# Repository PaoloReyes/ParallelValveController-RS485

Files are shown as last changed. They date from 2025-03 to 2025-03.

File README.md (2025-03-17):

# Parallel Valve Controller RS485 - README

## Overview
This repository contains the hardware and software needed to build a 20 container controller under freertos SMP multicore architecture on UART ISR event driven processes for ESP32-S3.
The controller is responsible for listening to RS485 messages and actuate the connected containers accordingly.

## Features
- **Parallel Control**: Uses two XTensa LX7 Cores under freertos on container independent tasks.
- **Reduces PLC overhead**: PID control is performed under the ESP32-S3 and not the main PLC logic.
- **Communication**: Interfaces with the main controller via RS485 communication.

## Communication Protocol
The car module receives and sends commands via a predefined protocol:
- `OP #` - Opens the controller based on its id number #.
- `CL` - Immediately closes the RS485 communication with the controller.
- `AD` - Returns the current id of the controller.
- `AD #` - Assigns the number # as the controller id.
- `WP` - Makes the AD # command to take effect and needs a reboot.
- `CV #1 #2 #3` - Performs a control update on the specified #1 container, #2 with the current weight and #3 the weight setpoint

## Hardware
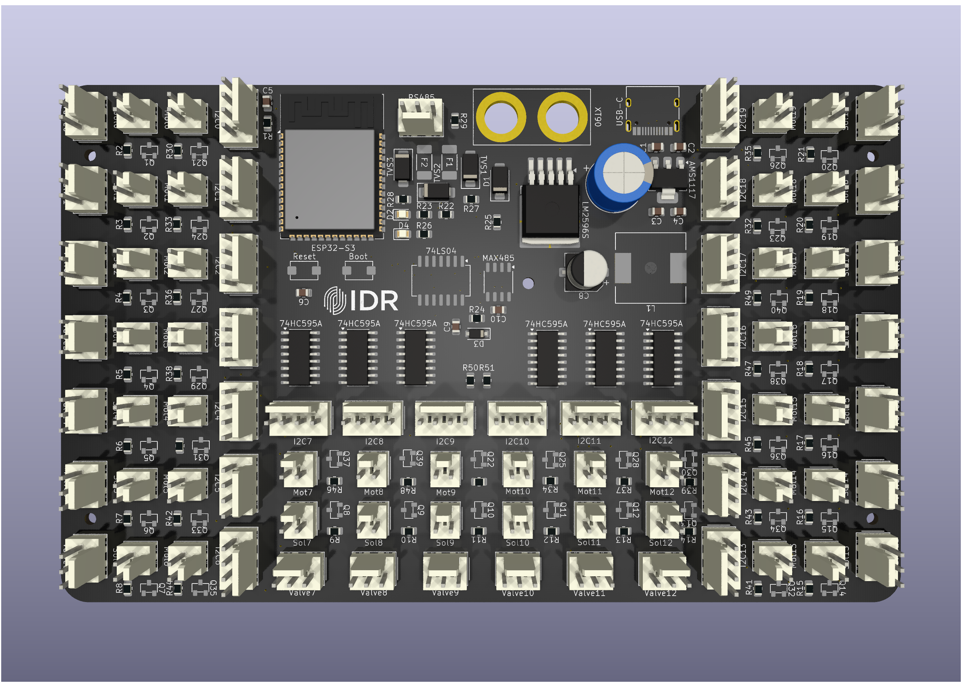
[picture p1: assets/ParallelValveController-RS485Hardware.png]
Hardware


## Software Architecture
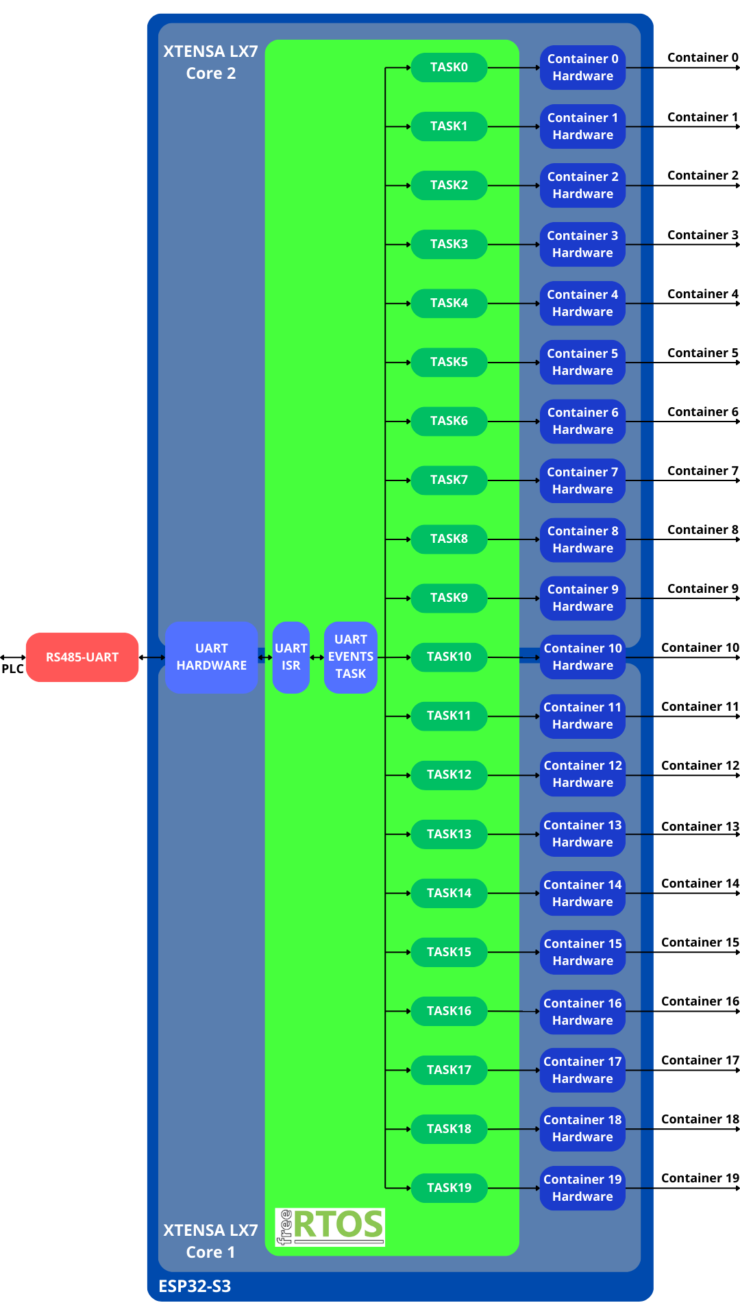
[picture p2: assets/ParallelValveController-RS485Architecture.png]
Controller


## FSM
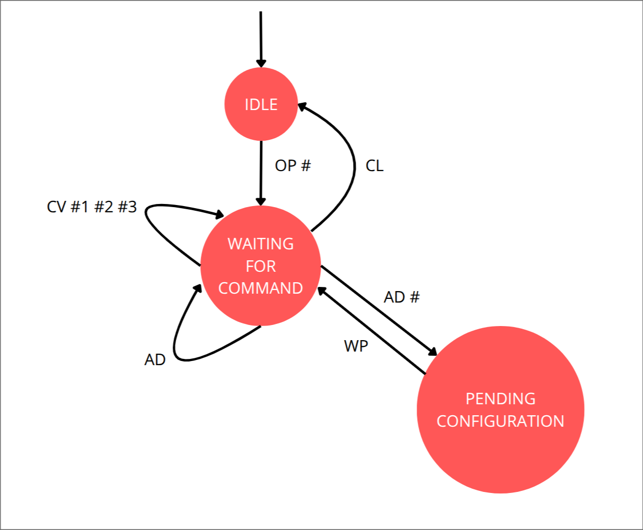
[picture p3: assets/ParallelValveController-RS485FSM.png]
FSM


## Troubleshooting
| Issue | Possible Cause | Solution |
|---|---|---|
| Valve not moving | Loose wiring, wrong valve firmware | Check connections, update your valve firmware |
| Solenoid not actuating | Loose wiring | Check connections |
| Motor not mixing | Loose wiring | Check connections |
| Container weight not available | Loose wiring, wrong digitalizer firmware | Check connections, update your valve firmware 
| No response | Communication failure, wrong firmware | Verify RS485 wiring and settings, update the controller firmware |

## Contributors
- **Paolo Reyes** - Lead Developer

## License
This project is licensed under the MIT License - see the LICENSE file for details.

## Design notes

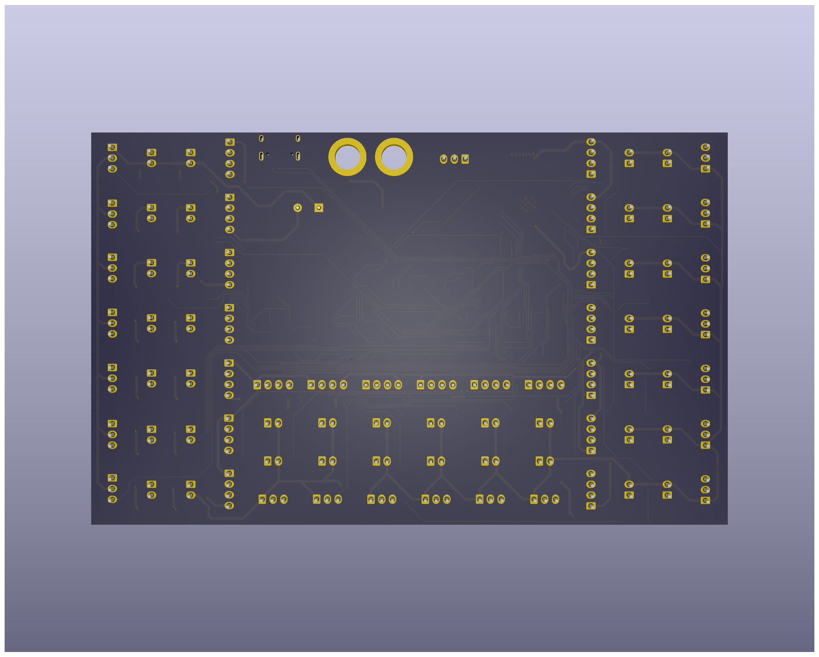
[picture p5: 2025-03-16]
Hardware/Renders/PreliminarBack.png

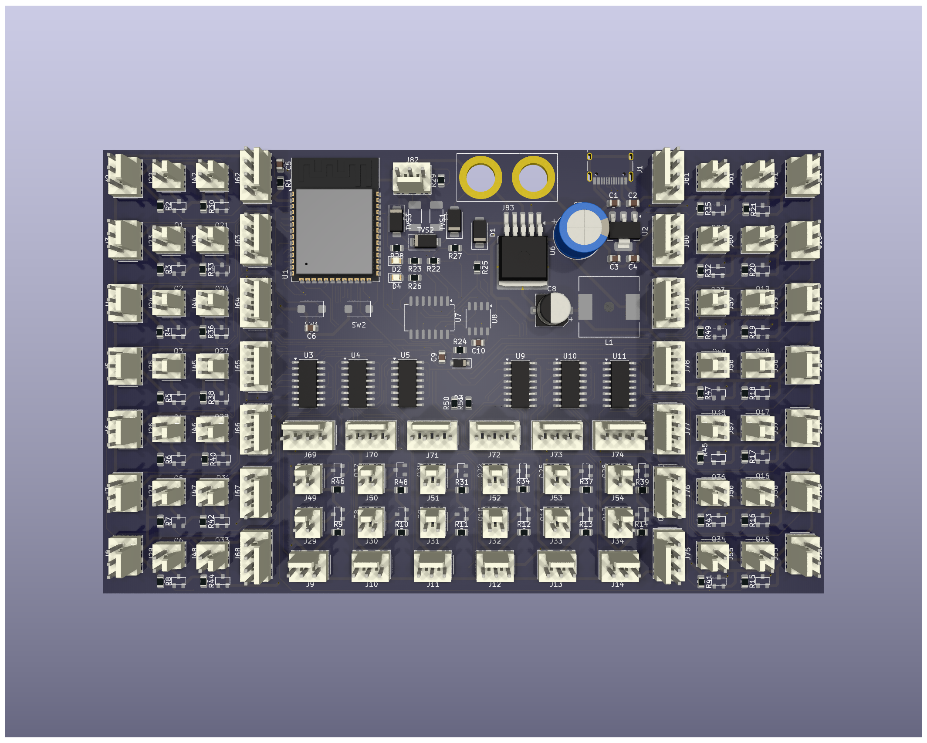
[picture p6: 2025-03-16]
Hardware/Renders/PreliminarFront.png

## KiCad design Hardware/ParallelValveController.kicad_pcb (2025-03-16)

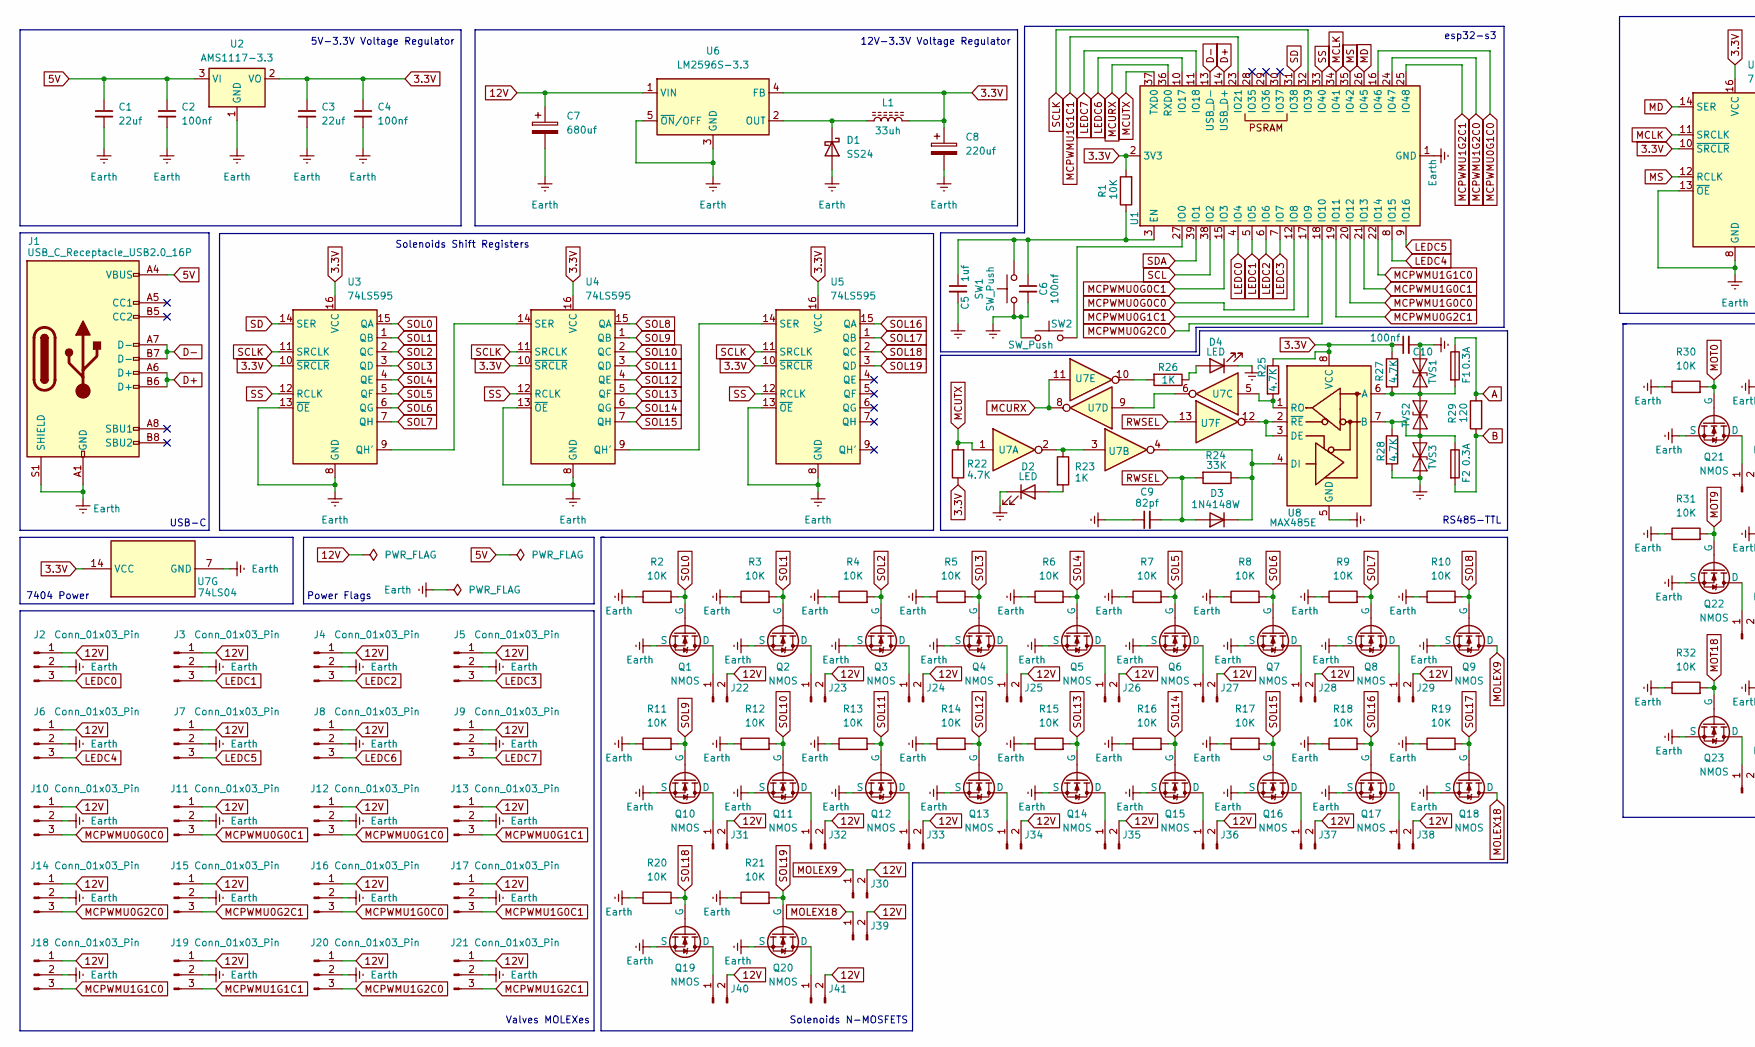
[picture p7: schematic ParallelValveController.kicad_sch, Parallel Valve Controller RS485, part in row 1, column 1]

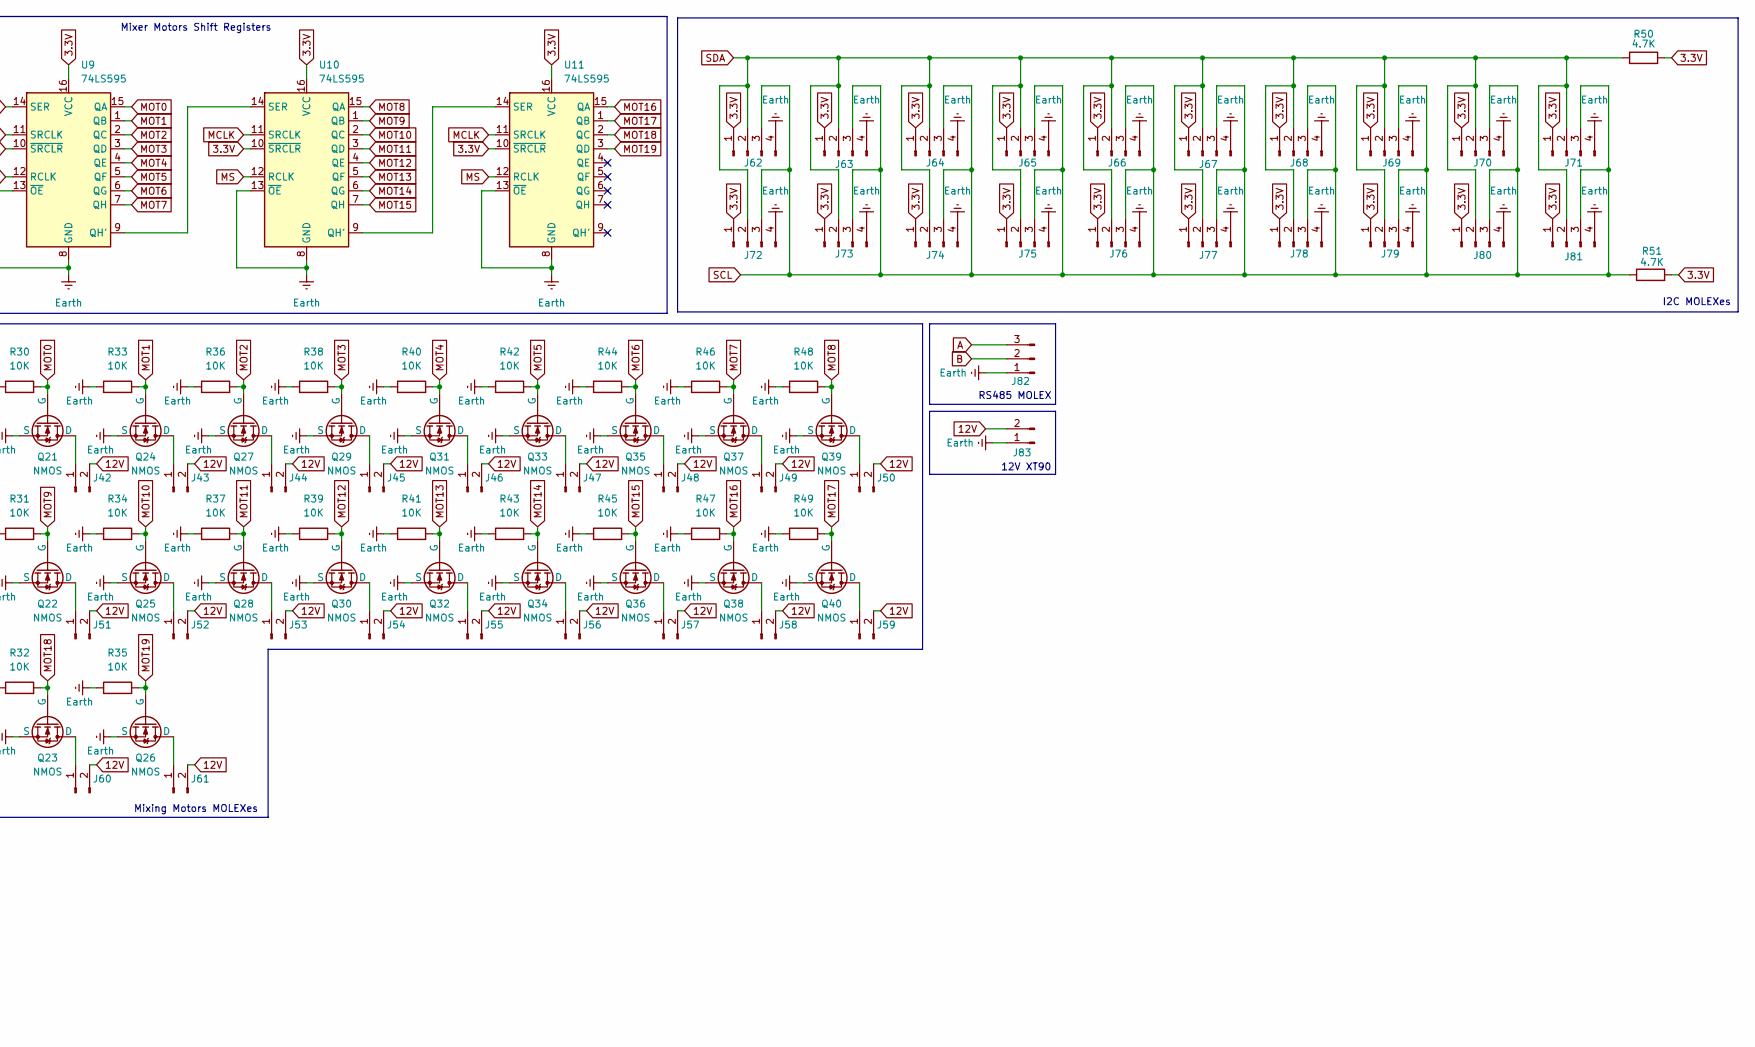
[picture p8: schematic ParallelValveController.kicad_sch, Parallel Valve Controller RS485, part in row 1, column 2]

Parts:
C1, C3: 22uf; C_0805_2012Metric
C2, C4, C6, C10: 100nf; C_0805_2012Metric
C5: 1uf; C_0805_2012Metric
C7: 680uf; CP_Radial_D10.0mm_P5.00mm
C8: 220uf; CP_Elec_6.3x7.7
C9: 82pf; C_0805_2012Metric
D1: SS24; D_SMA
D2, D4: LED; LED_0805_2012Metric
D3: 1N4148W; D_SOD-123
F1, F2: 0.3A; Fuse_2010_5025Metric_Pad1.52x2.65mm_HandSolder
J1: USB_C_Receptacle_USB2.0_16P; USB_C_Receptacle_HRO_TYPE-C-31-M-12
J2, J3, J4, J5, J6, J7, J8, J9, J10, J11, J12, J13, J14, J15, J16, J17, J18, J19, J20, J21, J82: Conn_01x03_Pin; Molex_KK-254_AE-6410-03A_1x03_P2.54mm_Vertical
J22, J23, J24, J25, J26, J27, J28, J29, J30, J31, J32, J33, J34, J35, J36, J37, J38, J39, J40, J41, J42, J43, J44, J45, J46, J47, J48, J49, J50, J51, J52, J53, J54, J55, J56, J57, J58, J59, J60, J61: Conn_01x02_Pin; Molex_KK-254_AE-6410-02A_1x02_P2.54mm_Vertical
J62, J63, J64, J65, J66, J67, J68, J69, J70, J71, J72, J73, J74, J75, J76, J77, J78, J79, J80, J81: Conn_01x02_Pin; Molex_KK-254_AE-6410-04A_1x04_P2.54mm_Vertical
J83: Conn_01x02_Pin; XT90-Female
L1: 33uh; L_12x12mm_H8mm
Q1, Q2, Q3, Q4, Q5, Q6, Q7, Q8, Q9, Q10, Q11, Q12, Q13, Q14, Q15, Q16, Q17, Q18, Q19, Q20, Q21, Q22, Q23, Q24, Q25, Q26, Q27, Q28, Q29, Q30, Q31, Q32, Q33, Q34, Q35, Q36, Q37, Q38, Q39, Q40: NMOS; SI2302
R1, R2, R3, R4, R5, R6, R7, R8, R9, R10, R11, R12, R13, R14, R15, R16, R17, R18, R19, R20, R21, R30, R31, R32, R33, R34, R35, R36, R37, R38, R39, R40, R41, R42, R43, R44, R45, R46, R47, R48, R49: 10K; R_0805_2012Metric
R22, R25, R27, R28, R50, R51: 4.7K; R_0805_2012Metric
R23, R26: 1K; R_0805_2012Metric
R24: 33K; R_0805_2012Metric
R29: 120; R_0805_2012Metric
SW1, SW2: SW_Push; MicroSwtich3x4x2mm
TVS1: SMAJ6.8CA; D_SMA
TVS2, TVS3: SMAJ6.5CA; D_SMA
U1: ESP32-S3-WROOM-1
U2: AMS1117-3.3; SOT-223-3_TabPin2
U3, U4, U5, U9, U10, U11: 74LS595; SOP-16_3.9x9.9mm_P1.27mm
U6: LM2596S-3.3; TO-263-5_TabPin3
U7: 74LS04; SO-14_5.3x10.2mm_P1.27mm
U8: MAX485E; SOP-8_3.9x4.9mm_P1.27mm

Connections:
3.3V: C3.1, C4.1, C8.1, C10.1, J62.1, J63.1, J64.1, J65.1, J66.1, J67.1, J68.1, J69.1, J70.1, J71.1, J72.1, J73.1, J74.1, J75.1, J76.1, J77.1, J78.1, J79.1, J80.1, J81.1, L1.2, R1.2, R22.1, R25.1, R27.1, R50.2, R51.2, U1.2 (3V3), U2.2 (VO), U3.10 (~SRCLR), U3.16 (VCC), U4.10 (~SRCLR), U4.16 (VCC), U5.10 (~SRCLR), U5.16 (VCC), U6.4 (FB), U7.14 (VCC), U8.8 (VCC), U9.10 (~SRCLR), U9.16 (VCC), U10.10 (~SRCLR), U10.16 (VCC), U11.10 (~SRCLR), U11.16 (VCC)
5V: C1.1, C2.1, J1.A4 (VBUS), J1.A9 (VBUS), J1.B4 (VBUS), J1.B9 (VBUS), U2.3 (VI)
12V: C7.1, J2.1, J3.1, J4.1, J5.1, J6.1, J7.1, J8.1, J9.1, J10.1, J11.1, J12.1, J13.1, J14.1, J15.1, J16.1, J17.1, J18.1, J19.1, J20.1, J21.1, J22.2, J23.2, J24.2, J25.2, J26.2, J27.2, J28.2, J29.2, J30.2, J31.2, J32.2, J33.2, J34.2, J35.2, J36.2, J37.2, J38.2, J39.2, J40.2, J41.2, J42.2, J43.2, J44.2, J45.2, J46.2, J47.2, J48.2, J49.2, J50.2, J51.2, J52.2, J53.2, J54.2, J55.2, J56.2, J57.2, J58.2, J59.2, J60.2, J61.2, J83.2, U6.1 (VIN)
A: F1.1, J82.3, R29.2
B: F2.2, J82.2, R29.1
D+: J1.A6 (D+), J1.B6 (D+), U1.14 (USB_D+)
D-: J1.A7 (D-), J1.B7 (D-), U1.13 (USB_D-)
Earth: C1.2, C2.2, C3.2, C4.2, C5.2, C6.2, C7.2, C8.2, C9.1, C10.2, D1.2 (A), D2.1 (K), D4.1 (K), J1.A1 (GND), J1.A12 (GND), J1.B1 (GND), J1.B12 (GND), J1.S1 (SHIELD), J2.2, J3.2, J4.2, J5.2, J6.2, J7.2, J8.2, J9.2, J10.2, J11.2, J12.2, J13.2, J14.2, J15.2, J16.2, J17.2, J18.2, J19.2, J20.2, J21.2, J62.4, J63.4, J64.4, J65.4, J66.4, J67.4, J68.4, J69.4, J70.4, J71.4, J72.4, J73.4, J74.4, J75.4, J76.4, J77.4, J78.4, J79.4, J80.4, J81.4, J82.1, J83.1, Q1.3 (S), Q2.3 (S), Q3.3 (S), Q4.3 (S), Q5.3 (S), Q6.3 (S), Q7.3 (S), Q8.3 (S), Q9.3 (S), Q10.3 (S), Q11.3 (S), Q12.3 (S), Q13.3 (S), Q14.3 (S), Q15.3 (S), Q16.3 (S), Q17.3 (S), Q18.3 (S), Q19.3 (S), Q20.3 (S), Q21.3 (S), Q22.3 (S), Q23.3 (S), Q24.3 (S), Q25.3 (S), Q26.3 (S), Q27.3 (S), Q28.3 (S), Q29.3 (S), Q30.3 (S), Q31.3 (S), Q32.3 (S), Q33.3 (S), Q34.3 (S), Q35.3 (S), Q36.3 (S), Q37.3 (S), Q38.3 (S), Q39.3 (S), Q40.3 (S), R2.1, R3.1, R4.1, R5.1, R6.1, R7.1, R8.1, R9.1, R10.1, R11.1, R12.1, R13.1, R14.1, R15.1, R16.1, R17.1, R18.1, R19.1, R20.1, R21.1, R28.2, R30.1, R31.1, R32.1, R33.1, R34.1, R35.1, R36.1, R37.1, R38.1, R39.1, R40.1, R41.1, R42.1, R43.1, R44.1, R45.1, R46.1, R47.1, R48.1, R49.1, SW1.1, SW2.1, TVS1.2 (A2), TVS3.1 (A1), U1.1 (GND), U1.40 (GND), U1.41 (GND), U2.1 (GND), U3.8 (GND), U3.13 (~OE), U4.8 (GND), U4.13 (~OE), U5.8 (GND), U5.13 (~OE), U6.3 (GND), U6.5 (~ON/OFF), U7.7 (GND), U8.5 (GND), U9.8 (GND), U9.13 (~OE), U10.8 (GND), U10.13 (~OE), U11.8 (GND), U11.13 (~OE)
LEDC0: J2.3, U1.4 (IO4)
LEDC1: J3.3, U1.5 (IO5)
LEDC2: J4.3, U1.6 (IO6)
LEDC3: J5.3, U1.7 (IO7)
LEDC4: J6.3, U1.8 (IO15)
LEDC5: J7.3, U1.9 (IO16)
LEDC6: J8.3, U1.10 (IO17)
LEDC7: J9.3, U1.11 (IO18)
MCLK: U1.34 (IO41), U9.11 (SRCLK), U10.11 (SRCLK), U11.11 (SRCLK)
MCPWMU0G0C0: J10.3, U1.12 (IO8)
MCPWMU0G0C1: J11.3, U1.15 (IO3)
MCPWMU0G1C0: J12.3, U1.16 (IO46)
MCPWMU0G1C1: J13.3, U1.17 (IO9)
MCPWMU0G2C0: J14.3, U1.18 (IO10)
MCPWMU0G2C1: J15.3, U1.19 (IO11)
MCPWMU1G0C0: J16.3, U1.20 (IO12)
MCPWMU1G0C1: J17.3, U1.21 (IO13)
MCPWMU1G1C0: J18.3, U1.22 (IO14)
MCPWMU1G1C1: J19.3, U1.23 (IO21)
MCPWMU1G2C0: J20.3, U1.24 (IO47)
MCPWMU1G2C1: J21.3, U1.25 (IO48)
MCURX: U1.36 (RXD0), U7.8, U7.11
MCUTX: R22.2, U1.37 (TXD0), U7.1
MD: U1.26 (IO45), U9.14 (SER)
MOLEX9: J30.1, Q9.1 (D)
MOLEX18: J39.1, Q18.1 (D)
MOT0: Q21.2 (G), R30.2, U9.15 (QA)
MOT1: Q24.2 (G), R33.2, U9.1 (QB)
MOT2: Q27.2 (G), R36.2, U9.2 (QC)
MOT3: Q29.2 (G), R38.2, U9.3 (QD)
MOT4: Q31.2 (G), R40.2, U9.4 (QE)
MOT5: Q33.2 (G), R42.2, U9.5 (QF)
MOT6: Q35.2 (G), R44.2, U9.6 (QG)
MOT7: Q37.2 (G), R46.2, U9.7 (QH)
MOT8: Q39.2 (G), R48.2, U10.15 (QA)
MOT9: Q22.2 (G), R31.2, U10.1 (QB)
MOT10: Q25.2 (G), R34.2, U10.2 (QC)
MOT11: Q28.2 (G), R37.2, U10.3 (QD)
MOT12: Q30.2 (G), R39.2, U10.4 (QE)
MOT13: Q32.2 (G), R41.2, U10.5 (QF)
MOT14: Q34.2 (G), R43.2, U10.6 (QG)
MOT15: Q36.2 (G), R45.2, U10.7 (QH)
MOT16: Q38.2 (G), R47.2, U11.15 (QA)
MOT17: Q40.2 (G), R49.2, U11.1 (QB)
MOT18: Q23.2 (G), R32.2, U11.2 (QC)
MOT19: Q26.2 (G), R35.2, U11.3 (QD)
MS: U1.35 (IO42), U9.12 (RCLK), U10.12 (RCLK), U11.12 (RCLK)
unnamed: D1.1 (K), L1.1, U6.2 (OUT)
unnamed: D2.2 (A), R23.2
unnamed: D3.1 (K), R24.1, U7.4, U8.4 (DI)
unnamed: D4.2 (A), R26.1
unnamed: J22.1, Q1.1 (D)
unnamed: J23.1, Q2.1 (D)
unnamed: J24.1, Q3.1 (D)
unnamed: J25.1, Q4.1 (D)
unnamed: J26.1, Q5.1 (D)
unnamed: J27.1, Q6.1 (D)
unnamed: J28.1, Q7.1 (D)
unnamed: J29.1, Q8.1 (D)
unnamed: J31.1, Q10.1 (D)
unnamed: J32.1, Q11.1 (D)
unnamed: J33.1, Q12.1 (D)
unnamed: J34.1, Q13.1 (D)
unnamed: J35.1, Q14.1 (D)
unnamed: J36.1, Q15.1 (D)
unnamed: J37.1, Q16.1 (D)
unnamed: J38.1, Q17.1 (D)
unnamed: J40.1, Q19.1 (D)
unnamed: J41.1, Q20.1 (D)
unnamed: J42.1, Q21.1 (D)
unnamed: J43.1, Q24.1 (D)
unnamed: J44.1, Q27.1 (D)
unnamed: J45.1, Q29.1 (D)
unnamed: J46.1, Q31.1 (D)
unnamed: J47.1, Q33.1 (D)
unnamed: J48.1, Q35.1 (D)
unnamed: J49.1, Q37.1 (D)
unnamed: J50.1, Q39.1 (D)
unnamed: J51.1, Q22.1 (D)
unnamed: J52.1, Q25.1 (D)
unnamed: J53.1, Q28.1 (D)
unnamed: J54.1, Q30.1 (D)
unnamed: J55.1, Q32.1 (D)
unnamed: J56.1, Q34.1 (D)
unnamed: J57.1, Q36.1 (D)
unnamed: J58.1, Q38.1 (D)
unnamed: J59.1, Q40.1 (D)
unnamed: J60.1, Q23.1 (D)
unnamed: J61.1, Q26.1 (D)
unnamed: R23.1, U7.2, U7.3
unnamed: R26.2, U7.10
unnamed: F1.2, R27.2, TVS1.1 (A1), TVS2.2 (A2), U8.6 (A)
unnamed: F2.1, R28.1, TVS2.1 (A1), TVS3.2 (A2), U8.7 (B)
unnamed: C5.1, C6.1, R1.1, SW1.2, U1.3 (EN)
unnamed: SW2.2, U1.27 (IO0)
unnamed: U3.9 (QH'), U4.14 (SER)
unnamed: U4.9 (QH'), U5.14 (SER)
unnamed: U7.6, U7.9
unnamed: U7.12, U8.2 (~RE), U8.3 (DE)
unnamed: R25.2, U7.5, U8.1 (RO)
unnamed: U10.9 (QH'), U11.14 (SER)
unnamed: U9.9 (QH'), U10.14 (SER)
RWSEL: C9.2, D3.2 (A), R24.2, U7.13
SCL: J62.3, J63.3, J64.3, J65.3, J66.3, J67.3, J68.3, J69.3, J70.3, J71.3, J72.3, J73.3, J74.3, J75.3, J76.3, J77.3, J78.3, J79.3, J80.3, J81.3, R51.1, U1.38 (IO2)
SCLK: U1.32 (IO39), U3.11 (SRCLK), U4.11 (SRCLK), U5.11 (SRCLK)
SD: U1.31 (IO38), U3.14 (SER)
SDA: J62.2, J63.2, J64.2, J65.2, J66.2, J67.2, J68.2, J69.2, J70.2, J71.2, J72.2, J73.2, J74.2, J75.2, J76.2, J77.2, J78.2, J79.2, J80.2, J81.2, R50.1, U1.39 (IO1)
SOL0: Q1.2 (G), R2.2, U3.15 (QA)
SOL1: Q2.2 (G), R3.2, U3.1 (QB)
SOL2: Q3.2 (G), R4.2, U3.2 (QC)
SOL3: Q4.2 (G), R5.2, U3.3 (QD)
SOL4: Q5.2 (G), R6.2, U3.4 (QE)
SOL5: Q6.2 (G), R7.2, U3.5 (QF)
SOL6: Q7.2 (G), R8.2, U3.6 (QG)
SOL7: Q8.2 (G), R9.2, U3.7 (QH)
SOL8: Q9.2 (G), R10.2, U4.15 (QA)
SOL9: Q10.2 (G), R11.2, U4.1 (QB)
SOL10: Q11.2 (G), R12.2, U4.2 (QC)
SOL11: Q12.2 (G), R13.2, U4.3 (QD)
SOL12: Q13.2 (G), R14.2, U4.4 (QE)
SOL13: Q14.2 (G), R15.2, U4.5 (QF)
SOL14: Q15.2 (G), R16.2, U4.6 (QG)
SOL15: Q16.2 (G), R17.2, U4.7 (QH)
SOL16: Q17.2 (G), R18.2, U5.15 (QA)
SOL17: Q18.2 (G), R19.2, U5.1 (QB)
SOL18: Q19.2 (G), R20.2, U5.2 (QC)
SOL19: Q20.2 (G), R21.2, U5.3 (QD)
SS: U1.33 (IO40), U3.12 (RCLK), U4.12 (RCLK), U5.12 (RCLK)

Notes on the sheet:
Solenoids Shift Registers
USB-C
RS485-TTL
Mixer Motors Shift Registers
RS485 MOLEX
12V XT90
esp32-s3
Valves MOLEXes
Mixing Motors MOLEXes
7404 Power
I2C MOLEXes
Power Flags
5V-3.3V Voltage Regulator
12V-3.3V Voltage Regulator
Solenoids N-MOSFETS

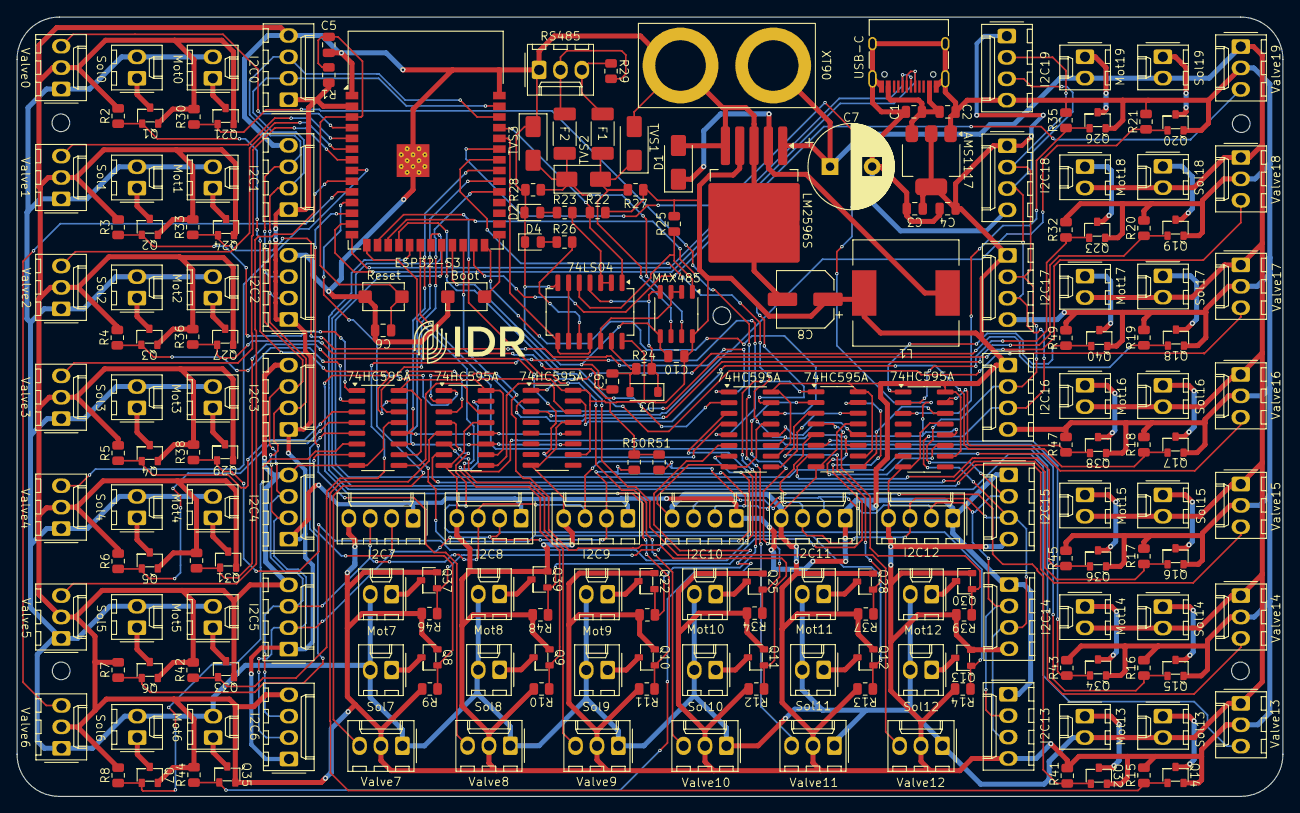
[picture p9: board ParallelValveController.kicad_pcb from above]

Board: 2 copper layers, 150.2 x 92.5 mm, 207 parts (0 on the bottom side), 136 nets.

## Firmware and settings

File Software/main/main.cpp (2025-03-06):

#include <freertos/FreeRTOS.h>
#include <freertos/task.h>
#include <freertos/queue.h>
#include <driver/uart.h>
#include <esp_log.h>
#include <nvs_flash.h>
#include <nvs.h>
#include <driver/ledc.h>
#include <driver/mcpwm.h>
#include "tasks/uart.h"
#include "tasks/pid.h"
#include "constants.h"
#include "data_types.h"

extern "C" void app_main(void) {
    // Set the log level for the UART task
    esp_log_level_set(UART_TAG, ESP_LOG_INFO);

    // Create a queue to handle UART event from ISR
    QueueHandle_t uart_queue;
    // UART Initialization
    uart_config_t uart_config = {
        .baud_rate = UART_BAUD_RATE,
        .data_bits = UART_DATA_8_BITS,
        .parity = UART_PARITY_DISABLE,
        .stop_bits = UART_STOP_BITS_1,
        .flow_ctrl = UART_HW_FLOWCTRL_DISABLE,
        .source_clk = UART_SCLK_DEFAULT,
    };
    // Set UART configuration parameters
    ESP_ERROR_CHECK(uart_param_config(UART_NUM, &uart_config));
    // Set UART pins
    ESP_ERROR_CHECK(uart_set_pin(UART_NUM, UART_PIN_NO_CHANGE, UART_PIN_NO_CHANGE, UART_PIN_NO_CHANGE, UART_PIN_NO_CHANGE));
    // Install UART driver using an event queue here
    ESP_ERROR_CHECK(uart_driver_install(UART_NUM, UART_BUFFER_SIZE, UART_BUFFER_SIZE, UART_QUEUE_SIZE, &uart_queue, 0));
    //Set uart pattern detect function.
    ESP_ERROR_CHECK(uart_enable_pattern_det_baud_intr(UART_NUM, '\n', 1, 9, 0, 0));
    //Reset the pattern queue length to record at most UART_QUEUE_SIZE pattern positions.
    ESP_ERROR_CHECK(uart_pattern_queue_reset(UART_NUM, UART_QUEUE_SIZE));

    //NVS Flash initialization
    ESP_ERROR_CHECK(nvs_flash_init());
    //Create a device data structure and nvs handle
    device_data_t device_data;
    //Open NVS
    ESP_ERROR_CHECK(nvs_open(DEVICE_DATA_NAMESPACE, NVS_READWRITE, &device_data.nvs_handle));
    //Read Address
    ESP_ERROR_CHECK(nvs_get_i32(device_data.nvs_handle, DEVICE_ADDRESS, &device_data.address));
    //Close
    nvs_close(device_data.nvs_handle);

    //ledc timer configuration
    ledc_timer_config_t ledc_timer = {
        .speed_mode = LEDC_LOW_SPEED_MODE,
        .duty_resolution = DUTY_RESOLUTION,
        .timer_num = LEDC_TIMER_0,
        .freq_hz = PWM_FREQ,
        .clk_cfg = LEDC_AUTO_CLK,
    };
    ESP_ERROR_CHECK(ledc_timer_config(&ledc_timer));
    //Create an array for ledc channels
    ledc_channel_config_t ledc_channels[8];
    //ledc channel0 configuration and defaults angle to 0
    ledc_channels[0] = {
        .gpio_num = VALVE0_PIN,
        .speed_mode = LEDC_LOW_SPEED_MODE,
        .channel = VALVE0_CHANNEL,
        .intr_type = LEDC_INTR_DISABLE,
        .timer_sel = LEDC_TIMER_0,
        .duty = 0,
        .hpoint = 0,
        .sleep_mode = LEDC_SLEEP_MODE_NO_ALIVE_NO_PD,
    };
    ESP_ERROR_CHECK(ledc_channel_config(&ledc_channels[0]));
    write_ledc_angle(ledc_channels[0].channel, 0);

    //Create an array for pins and channels
    gpio_num_t valve_pins_ledc[7] = {VALVE1_PIN, VALVE2_PIN, VALVE3_PIN, VALVE4_PIN, VALVE5_PIN, VALVE6_PIN, VALVE7_PIN};
    ledc_channel_t valve_channels_ledc[7] = {VALVE1_CHANNEL, VALVE2_CHANNEL, VALVE3_CHANNEL, VALVE4_CHANNEL, VALVE5_CHANNEL, VALVE6_CHANNEL, VALVE7_CHANNEL};
    //Copy the ledc_channel0 configuration to other ledc_channels configuration, update pin and channel, apply configurations and default angles
    for (int i = 1; i < 8; i++){
        memcpy(&ledc_channels[i], &ledc_channels[0], sizeof(ledc_channel_config_t));
        ledc_channels[i].gpio_num = valve_pins_ledc[i-1];
        ledc_channels[i].channel = valve_channels_ledc[i-1];
        ESP_ERROR_CHECK(ledc_channel_config(&ledc_channels[i]));
        write_ledc_angle(ledc_channels[i].channel, 0);
    }

    //Create an array for mcwpm pins
    gpio_num_t valve_pins_mcpwm0[6] = {VALVE8_PIN, VALVE9_PIN, VALVE10_PIN, VALVE11_PIN, VALVE12_PIN, VALVE13_PIN};
    gpio_num_t valve_pins_mcpwm1[6] = {VALVE14_PIN, VALVE15_PIN, VALVE16_PIN, VALVE17_PIN, VALVE18_PIN, VALVE19_PIN};
    //Initializa the mcpwm modules
    for (int i = 0; i < 6; i++){
        ESP_ERROR_CHECK(mcpwm_gpio_init(MCPWM_UNIT_0, (mcpwm_io_signals_t)i, valve_pins_mcpwm0[i]));
        ESP_ERROR_CHECK(mcpwm_gpio_init(MCPWM_UNIT_1, (mcpwm_io_signals_t)i, valve_pins_mcpwm1[i]));
    }
    //Create a configuration for the mcpwm timers
    mcpwm_config_t pwm_config = {
        .frequency = PWM_FREQ,
        .cmpr_a = 0,
        .cmpr_b = 0,
        .duty_mode = MCPWM_DUTY_MODE_0,
        .counter_mode = MCPWM_UP_COUNTER,
    };
    //Initialize the mcpwm timers, each timer will control two operators
    ESP_ERROR_CHECK(mcpwm_init(MCPWM_UNIT_0, MCPWM_TIMER_0, &pwm_config));
    ESP_ERROR_CHECK(mcpwm_init(MCPWM_UNIT_0, MCPWM_TIMER_1, &pwm_config));
    ESP_ERROR_CHECK(mcpwm_init(MCPWM_UNIT_0, MCPWM_TIMER_2, &pwm_config));
    ESP_ERROR_CHECK(mcpwm_init(MCPWM_UNIT_1, MCPWM_TIMER_0, &pwm_config));
    ESP_ERROR_CHECK(mcpwm_init(MCPWM_UNIT_1, MCPWM_TIMER_1, &pwm_config));
    ESP_ERROR_CHECK(mcpwm_init(MCPWM_UNIT_1, MCPWM_TIMER_2, &pwm_config));
    //Set the initial angle to 0 for all the mcpwm operators
    for (int i = 0; i < 6; i++){
        write_mcpwm_angle(MCPWM_UNIT_0, (mcpwm_io_signals_t)i, 0);
        write_mcpwm_angle(MCPWM_UNIT_1, (mcpwm_io_signals_t)i, 0);
    }

    //Create an array of PID task functions to create the tasks in a loop
    TaskFunction_t PID_tasks[20] = {PID_task_0, PID_task_1, PID_task_2, PID_task_3, PID_task_4, 
        PID_task_5, PID_task_6, PID_task_7, PID_task_8, PID_task_9, 
        PID_task_10, PID_task_11, PID_task_12, PID_task_13, PID_task_14, 
        PID_task_15, PID_task_16, PID_task_17, PID_task_18, PID_task_19};
    //Create an array of names for the PID tasks to create the tasks in a loop
    const char* PID_tasks_names[20] = {"PID_task_0", "PID_task_1", "PID_task_2", "PID_task_3", "PID_task_4", 
            "PID_task_5", "PID_task_6", "PID_task_7", "PID_task_8", "PID_task_9", 
            "PID_task_10", "PID_task_11", "PID_task_12", "PID_task_13", "PID_task_14", 
            "PID_task_15", "PID_task_16", "PID_task_17", "PID_task_18", "PID_task_19"};
    //Create an array of pid_task_data_t for the PID tasks
    pid_task_data_t pid_task_data[20];
    //Fill ledc data
    for (int i = 0; i < 8; i++){
        pid_task_data[i].ledc_channel = ledc_channels[i].channel;
        pid_task_data[i].is_ledc = true;
    }
    //Fill mcpwm data
    for (int i = 8; i < 14; i++){
        pid_task_data[i].mcpwm_unit = MCPWM_UNIT_0;
        pid_task_data[i].mcpwm_io_signal = (mcpwm_io_signals_t)(i-8);
        pid_task_data[i].is_ledc = false;
    }
    for (int i = 14; i < 20; i++){
        pid_task_data[i].mcpwm_unit = MCPWM_UNIT_1;
        pid_task_data[i].mcpwm_io_signal = (mcpwm_io_signals_t)(i-14);
        pid_task_data[i].is_ledc = false;
    }
    //Create a task handle array for PID tasks
    TaskHandle_t* pid_tasks = (TaskHandle_t*)malloc(sizeof(TaskHandle_t)*20); 
    //Create individual tasks for PID control for multicore processing
    for (int i = 0; i < 20; i++){
        xTaskCreatePinnedToCore(PID_tasks[i], PID_tasks_names[i], 4096, &pid_task_data[i], 1, &pid_tasks[i], tskNO_AFFINITY);
    }

    //Create an uart task data structure
    uart_task_data_t uart_task_data = {
        .device_data = device_data,
        .uart_queue = uart_queue,
        .pid_tasks = pid_tasks,
    };

    //Create a task to handle UART event from ISR
    xTaskCreatePinnedToCore(uart_event_task, "uart_event_task", 8192, (void*)&uart_task_data, 2, NULL, tskNO_AFFINITY);
}

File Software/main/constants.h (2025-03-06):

#define UART_NUM UART_NUM_0   //UART number
#define UART_BUFFER_SIZE 256  //Size of the UART buffer
#define UART_BAUD_RATE 115200 //Baud rate for the UART
#define UART_QUEUE_SIZE 10    //Size of the UART queue

#define UART_TAG "UART" //TAG for the UART tasks
#define PID_TAG "PID"   //TAG for the PID tasks
#define NVS_TAG "NVS"   //TAG for the NVS

#define DEVICE_DATA_NAMESPACE "device_data"  //Namespace for the device data in the NVS
#define DEVICE_ADDRESS        "address"      //Address of the key value pair in the NVS for the device address

#define PWM_FREQ 50                       //PWM frequency
#define DUTY_RESOLUTION LEDC_TIMER_14_BIT //PWM resolution
//Define the pins and channels for the valves using the LEDC peripheral
#define VALVE0_PIN GPIO_NUM_4
#define VALVE0_CHANNEL LEDC_CHANNEL_0
#define VALVE1_PIN GPIO_NUM_5
#define VALVE1_CHANNEL LEDC_CHANNEL_1
#define VALVE2_PIN GPIO_NUM_6
#define VALVE2_CHANNEL LEDC_CHANNEL_2
#define VALVE3_PIN GPIO_NUM_7
#define VALVE3_CHANNEL LEDC_CHANNEL_3
#define VALVE4_PIN GPIO_NUM_15
#define VALVE4_CHANNEL LEDC_CHANNEL_4
#define VALVE5_PIN GPIO_NUM_16
#define VALVE5_CHANNEL LEDC_CHANNEL_5
#define VALVE6_PIN GPIO_NUM_17
#define VALVE6_CHANNEL LEDC_CHANNEL_6
#define VALVE7_PIN GPIO_NUM_18
#define VALVE7_CHANNEL LEDC_CHANNEL_7
//Define the pins for the valves using the MCPWM peripheral
#define VALVE8_PIN GPIO_NUM_8
#define VALVE9_PIN GPIO_NUM_3
#define VALVE10_PIN GPIO_NUM_46
#define VALVE11_PIN GPIO_NUM_9
#define VALVE12_PIN GPIO_NUM_10
#define VALVE13_PIN GPIO_NUM_11
#define VALVE14_PIN GPIO_NUM_12
#define VALVE15_PIN GPIO_NUM_13
#define VALVE16_PIN GPIO_NUM_14
#define VALVE17_PIN GPIO_NUM_21
#define VALVE18_PIN GPIO_NUM_47
#define VALVE19_PIN GPIO_NUM_48

#define VALVE0_KP 1.0
#define VALVE0_KI 0.0
#define VALVE0_KD 0.0

#define VALVE1_KP 1.0
#define VALVE1_KI 0.0
#define VALVE1_KD 0.0

#define VALVE2_KP 1.0
#define VALVE2_KI 0.0
#define VALVE2_KD 0.0

#define VALVE3_KP 1.0
#define VALVE3_KI 0.0
#define VALVE3_KD 0.0

#define VALVE4_KP 1.0
#define VALVE4_KI 0.0
#define VALVE4_KD 0.0

#define VALVE5_KP 1.0
#define VALVE5_KI 0.0
#define VALVE5_KD 0.0

#define VALVE6_KP 1.0
#define VALVE6_KI 0.0
#define VALVE6_KD 0.0

#define VALVE7_KP 1.0
#define VALVE7_KI 0.0
#define VALVE7_KD 0.0

#define VALVE8_KP 1.0
#define VALVE8_KI 0.0
#define VALVE8_KD 0.0

#define VALVE9_KP 1.0
#define VALVE9_KI 0.0
#define VALVE9_KD 0.0

#define VALVE10_KP 1.0
#define VALVE10_KI 0.0
#define VALVE10_KD 0.0

#define VALVE11_KP 1.0
#define VALVE11_KI 0.0
#define VALVE11_KD 0.0

#define VALVE12_KP 1.0
#define VALVE12_KI 0.0
#define VALVE12_KD 0.0

#define VALVE13_KP 1.0
#define VALVE13_KI 0.0
#define VALVE13_KD 0.0

#define VALVE14_KP 1.0
#define VALVE14_KI 0.0
#define VALVE14_KD 0.0

#define VALVE15_KP 1.0
#define VALVE15_KI 0.0
#define VALVE15_KD 0.0

#define VALVE16_KP 1.0
#define VALVE16_KI 0.0
#define VALVE16_KD 0.0

#define VALVE17_KP 1.0
#define VALVE17_KI 0.0
#define VALVE17_KD 0.0

#define VALVE18_KP 1.0
#define VALVE18_KI 0.0
#define VALVE18_KD 0.0

#define VALVE19_KP 1.0
#define VALVE19_KI 0.0
#define VALVE19_KD 0.0

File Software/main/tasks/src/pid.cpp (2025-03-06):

#include "../pid.h"

static std::map<mcpwm_io_signals_t, mcpwm_generator_t> mcpwm_io2generator = {
    {MCPWM0A, MCPWM_GEN_A},
    {MCPWM0B, MCPWM_GEN_B},
    {MCPWM1A, MCPWM_GEN_A},
    {MCPWM1B, MCPWM_GEN_B},
    {MCPWM2A, MCPWM_GEN_A},
    {MCPWM2B, MCPWM_GEN_B},
};

static std::map<mcpwm_io_signals_t, mcpwm_timer_t> mcpwm_io2timer = {
    {MCPWM0A, MCPWM_TIMER_0},
    {MCPWM0B, MCPWM_TIMER_0},
    {MCPWM1A, MCPWM_TIMER_1},
    {MCPWM1B, MCPWM_TIMER_1},
    {MCPWM2A, MCPWM_TIMER_2},
    {MCPWM2B, MCPWM_TIMER_2},
};

/// @brief Perform the control on valve0
/// @param pvParameters Void poiner to usefull data for the task
void PID_task_0(void* pvParameters){
    pid_task_data_t pid_task_data = *((pid_task_data_t*)pvParameters);
    PID_controller pid_controller(VALVE0_KP, VALVE0_KI, VALVE0_KD);
    for (;;) {
        wait_notification_and_compute(&pid_task_data, &pid_controller, 0);
    }
    free(&pid_task_data);
    vTaskDelete(NULL);
}

/// @brief Perform the control on valve1
/// @param pvParameters Void poiner to usefull data for the task
void PID_task_1(void* pvParameters){
    pid_task_data_t pid_task_data = *((pid_task_data_t*)pvParameters);
    PID_controller pid_controller(VALVE1_KP, VALVE1_KI, VALVE1_KD);
    for (;;) {
        wait_notification_and_compute(&pid_task_data, &pid_controller, 1);
    }
    free(&pid_task_data);
    vTaskDelete(NULL);
}

/// @brief Perform the control on valve2
/// @param pvParameters Void poiner to usefull data for the task
void PID_task_2(void* pvParameters){
    pid_task_data_t pid_task_data = *((pid_task_data_t*)pvParameters);
    PID_controller pid_controller(VALVE2_KP, VALVE2_KI, VALVE2_KD);
    for (;;) {
        wait_notification_and_compute(&pid_task_data, &pid_controller, 2);
    }
    free(&pid_task_data);
    vTaskDelete(NULL);
}

/// @brief Perform the control on valve3
/// @param pvParameters Void poiner to usefull data for the task
void PID_task_3(void* pvParameters){
    pid_task_data_t pid_task_data = *((pid_task_data_t*)pvParameters);
    PID_controller pid_controller(VALVE3_KP, VALVE3_KI, VALVE3_KD);
    for (;;) {
        wait_notification_and_compute(&pid_task_data, &pid_controller, 3);
    }
    free(&pid_task_data);
    vTaskDelete(NULL);
}

/// @brief Perform the control on valve4
/// @param pvParameters Void poiner to usefull data for the task
void PID_task_4(void* pvParameters){
    pid_task_data_t pid_task_data = *((pid_task_data_t*)pvParameters);
    PID_controller pid_controller(VALVE4_KP, VALVE4_KI, VALVE4_KD);
    for (;;) {
        wait_notification_and_compute(&pid_task_data, &pid_controller, 4);
    }
    free(&pid_task_data);
    vTaskDelete(NULL);
}

/// @brief Perform the control on valve5
/// @param pvParameters Void poiner to usefull data for the task
void PID_task_5(void* pvParameters){
    pid_task_data_t pid_task_data = *((pid_task_data_t*)pvParameters);
    PID_controller pid_controller(VALVE5_KP, VALVE5_KI, VALVE5_KD);
    for (;;) {
        wait_notification_and_compute(&pid_task_data, &pid_controller, 5);
    }
    free(&pid_task_data);
    vTaskDelete(NULL);
}

/// @brief Perform the control on valve6
/// @param pvParameters Void poiner to usefull data for the task
void PID_task_6(void* pvParameters){
    pid_task_data_t pid_task_data = *((pid_task_data_t*)pvParameters);
    PID_controller pid_controller(VALVE6_KP, VALVE6_KI, VALVE6_KD);
    for (;;) {
        wait_notification_and_compute(&pid_task_data, &pid_controller, 6);
    }
    free(&pid_task_data);
    vTaskDelete(NULL);
}

/// @brief Perform the control on valve7
/// @param pvParameters Void poiner to usefull data for the task
void PID_task_7(void* pvParameters){
    pid_task_data_t pid_task_data = *((pid_task_data_t*)pvParameters);
    PID_controller pid_controller(VALVE7_KP, VALVE7_KI, VALVE7_KD);
    for (;;) {
        wait_notification_and_compute(&pid_task_data, &pid_controller, 7);
    }
    free(&pid_task_data);
    vTaskDelete(NULL);
}

/// @brief Perform the control on valve8
/// @param pvParameters Void poiner to usefull data for the task
void PID_task_8(void* pvParameters){
    pid_task_data_t pid_task_data = *((pid_task_data_t*)pvParameters);
    PID_controller pid_controller(VALVE8_KP, VALVE8_KI, VALVE8_KD);
    for (;;) {
        wait_notification_and_compute(&pid_task_data, &pid_controller, 8);
    }
    free(&pid_task_data);
    vTaskDelete(NULL);
}

/// @brief Perform the control on valve9
/// @param pvParameters Void poiner to usefull data for the task
void PID_task_9(void* pvParameters){
    pid_task_data_t pid_task_data = *((pid_task_data_t*)pvParameters);
    PID_controller pid_controller(VALVE9_KP, VALVE9_KI, VALVE9_KD);
    for (;;) {
        wait_notification_and_compute(&pid_task_data, &pid_controller, 9);
    }
    free(&pid_task_data);
    vTaskDelete(NULL);
}

/// @brief Perform the control on valve10
/// @param pvParameters Void poiner to usefull data for the task
void PID_task_10(void* pvParameters){
    pid_task_data_t pid_task_data = *((pid_task_data_t*)pvParameters);
    PID_controller pid_controller(VALVE10_KP, VALVE10_KI, VALVE10_KD);
    for (;;) {
        wait_notification_and_compute(&pid_task_data, &pid_controller, 10);
    }
    free(&pid_task_data);
    vTaskDelete(NULL);
}

/// @brief Perform the control on valve11
/// @param pvParameters Void poiner to usefull data for the task
void PID_task_11(void* pvParameters){
    pid_task_data_t pid_task_data = *((pid_task_data_t*)pvParameters);
    PID_controller pid_controller(VALVE11_KP, VALVE11_KI, VALVE11_KD);
    for (;;) {
        wait_notification_and_compute(&pid_task_data, &pid_controller, 11);
    }
    free(&pid_task_data);
    vTaskDelete(NULL);
}

/// @brief Perform the control on valve12
/// @param pvParameters Void poiner to usefull data for the task
void PID_task_12(void* pvParameters){
    pid_task_data_t pid_task_data = *((pid_task_data_t*)pvParameters);
    PID_controller pid_controller(VALVE12_KP, VALVE12_KI, VALVE12_KD);
    for (;;) {
        wait_notification_and_compute(&pid_task_data, &pid_controller, 12);
    }
    free(&pid_task_data);
    vTaskDelete(NULL);
}

/// @brief Perform the control on valve13
/// @param pvParameters Void poiner to usefull data for the task
void PID_task_13(void* pvParameters){
    pid_task_data_t pid_task_data = *((pid_task_data_t*)pvParameters);
    PID_controller pid_controller(VALVE13_KP, VALVE13_KI, VALVE13_KD);
    for (;;) {
        wait_notification_and_compute(&pid_task_data, &pid_controller, 13);
    }
    free(&pid_task_data);
    vTaskDelete(NULL);
}
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

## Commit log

2025-03-04 feat(Release): UART FSM and multicore tasks infrastructure
2025-03-05 feat(PID Tasks): Task Notifications to PID tasks
2025-03-05 feat(PID Tasks): Infrastructure to output pwm from ledc module via second param on task notifications
2025-03-06 feat(mcpwm): Infrastructure to output pwm from mcpwm unit 0
2025-03-06 feat(PID): Added support for mcpwm on 12 new PID Tasks
2025-03-06 feat(PID): Added pid controller for each task
2025-03-06 fix(ESP_ERROR_CHECK): Added some ESP_ERROR_CHECKS on missing functions
    [main.cpp, pid.cpp]
2025-03-16 feat(Hardware): Hardware implementation
    [ParallelValveController-B_Cu.gbr, ParallelValveController-B_Mask.gbr, ParallelValveController-B_Paste.gbr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]
